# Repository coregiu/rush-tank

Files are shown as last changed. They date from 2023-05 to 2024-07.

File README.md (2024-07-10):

# Rush Tank
Rush Tank(简称Ruke)是利用51单片机、L298N电机驱动、PS2手柄、坦克坦克底盘、1000RPM的带霍尔效应编码器的JGB37 520调速电机DIY实现的PS2摇控坦克，提供精确速度控制，加减速，遥控体验绝佳。

## 功能说明
#### 遥控坦克正常行驶
可通过PS2左侧摇杆控制坦克前进、后退、左转、右转。

#### 加减速控制
可通过PS2右侧摇杆控制坦克加速、减速、向左前行进、向右前行进。

## 设计说明

#### 硬件设计

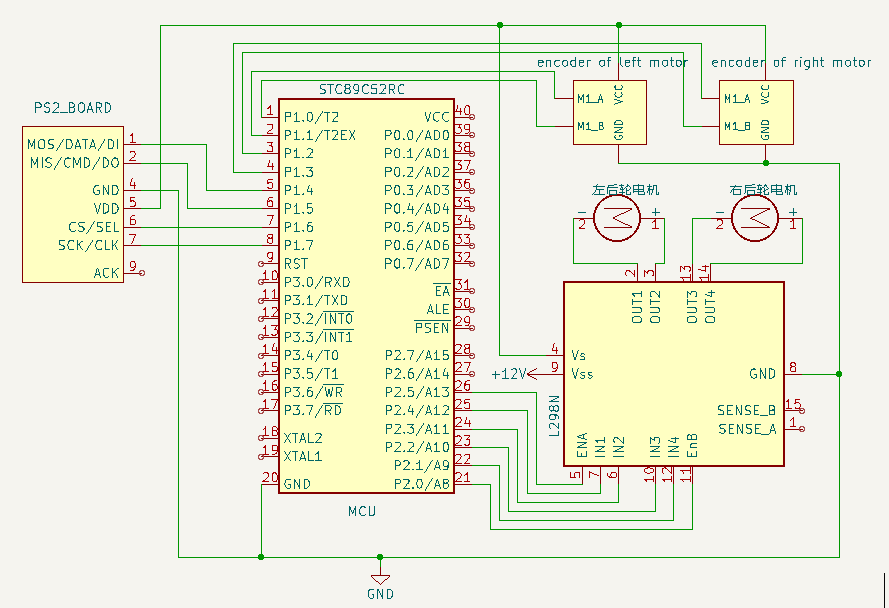
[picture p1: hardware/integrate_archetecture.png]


详细参照：[硬件设计说明](hardware/README.md)

#### 软件设计
##### 实现原理及状态图
如硬件设计所示，RUKE采用两组电机控制，使用L298N电机驱动控制实现RUKE行驶控制。采用PS2手柄作为控制输入。
因此，RUKE实现原理就是将PS2命令接收转换成控制L298N的信号即完成RUKE行驶控制。

L298N分两路电机控制，每路电机有三个信号引脚： 输入1（后文叫FRONT），输入2（后文叫BACK），使能（后文叫ENABLE）。
控制状态如下：
- 输入1=1， 输入2=0， 前进方向。 使能引脚默认接高电平，也可通过PWM控制速度。
- 输入1=0， 输入2=1， 后退方向。
- 输入1=0， 输入2=0， 停止。

因此RUKE实现逻辑是：
- 前进：两个电机都前进方向，使能全部高电平。
- 后退：两个电机都后退方向，使能全部高电平。
- 左转：左侧电机停止，右侧电机前进。
- 右转：右侧电机停止，左侧电机前进。
- 左向调头：左侧电机后退，右侧电机前进。
- 右向调头：右侧电机后退，左侧电机前进。
- 调速、左右向微调都是通过对ENABLE信号脚进行PWM控制实现速度微调。

因此，RUKE状态设计如下图，分小车行驶方向状态、速度状态两种状态，分别由PS2左、右两侧摇杆控制：
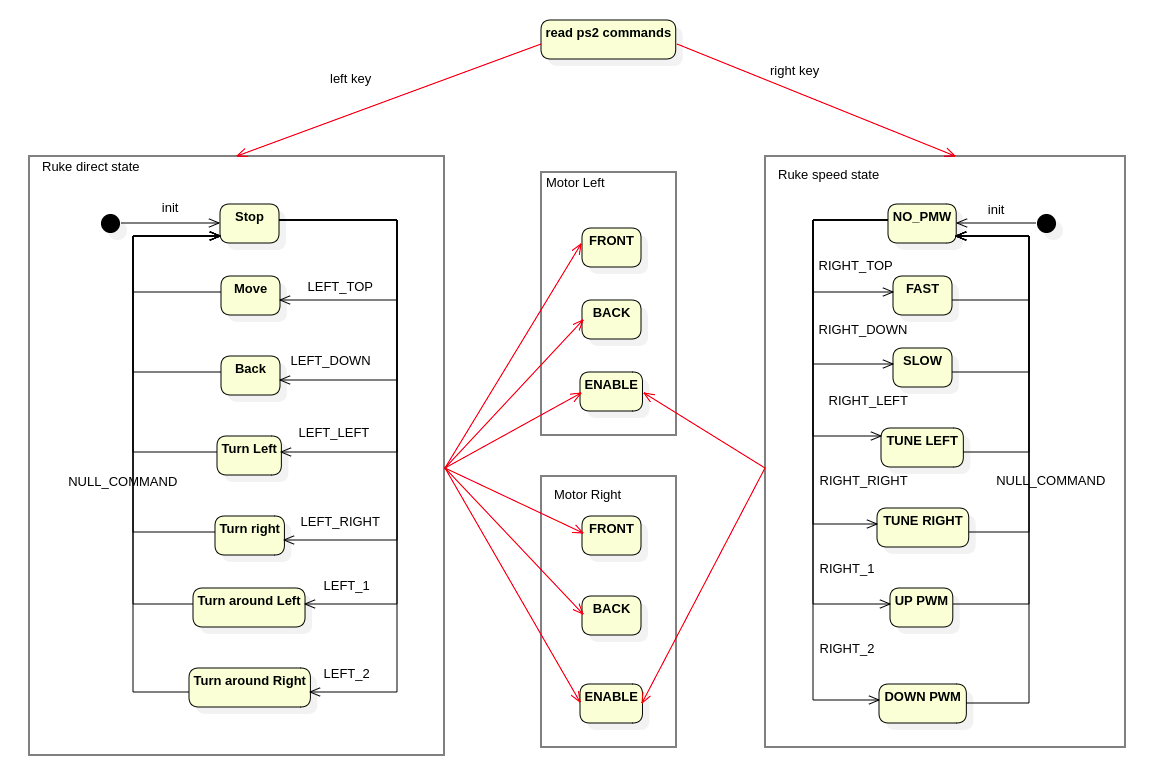
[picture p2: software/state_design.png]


##### 详细类图设计
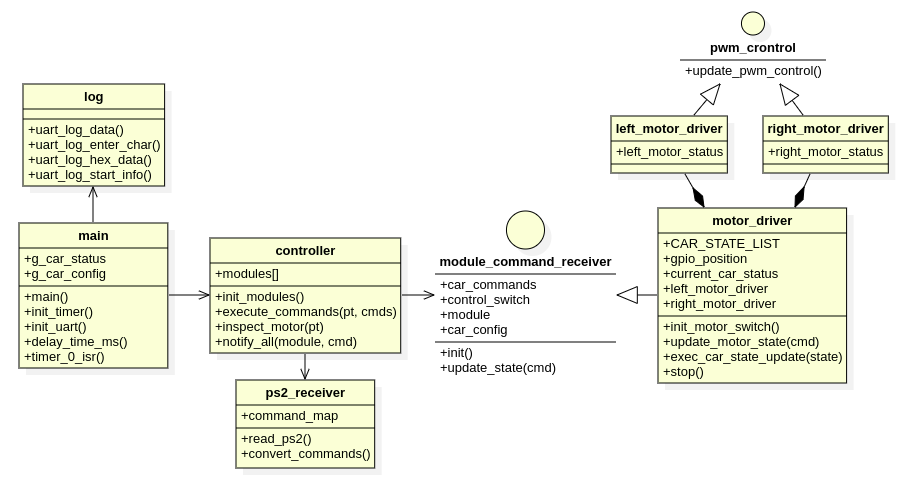
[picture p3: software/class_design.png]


详细参照：[软件设计说明和代码](software/README.md)

## PS2按键功能

| 按键 | 功能 | 监控指示灯 |
| --- | --- | --- |
| 左侧上键 | 坦克前进，长按有效，放开停止 | P0_0 |
| 左侧下键 | 坦克后退，长按有效，放开停止 | P0_1 |
| 左侧左键 | 坦克左转，长按有效，放开停止 | P0_2 |
| 左侧右键 | 坦克右转，长按有效，放开停止 | P0_3 |
| 左侧1键  | 顺时针快速调头 | P0_4 |
| 左侧2键  | 逆时针快速调头 | P0_5 |
| 右侧上健 | 加速行驶 | P0_0 |
| 右侧下键 | 减速行驶 | P0_1 |
| 右侧左键 | 坦克向左微调80%PWM，长按有效，放开恢复正常行驶  | P0_2 |
| 右侧右键 | 坦克向右微调80%PWM，长按有效，放开恢复正常行驶  | P0_3 |
| 右侧1键  | 同时按住左侧健时，直接最大速度行驶。 不按左侧健时，微调行驶角度，PWN加20% | P0_4 |
| 右侧2键  | 同时按住左侧健时，直接最小速度行驶。 不按左侧健时，微调行驶角度，PWN减20% | P0_5 |

## 成品效果

##### 视频

https://www.bilibili.com/video/BV1Zu411p7aM/?spm_id_from=333.999.0.0

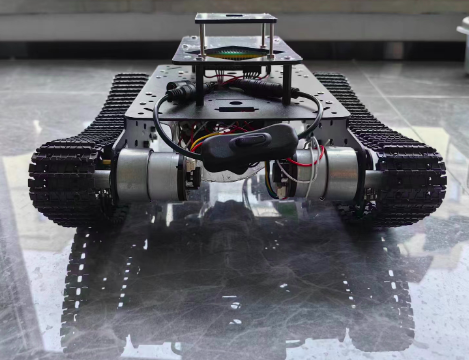
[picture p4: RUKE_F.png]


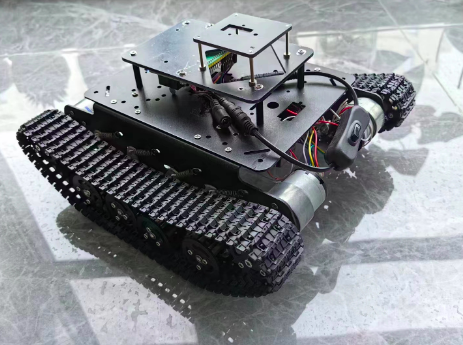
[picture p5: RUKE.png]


## 硬件模块及工具清单：

| 模块 | 说明 | 价格(元) |
| --- | --- | --- |
| 51单片机 | 单片机 STC89C52RC芯片，11.0592晶振。 | 40 |
| 坦克底盘 | 坦克底盘及M3铜柱螺丝若干，底盘带4个直流电机。 | 350 |
| ps2手柄 | 无线的那种，会带接收器。 | 40 |
| L298N电机驱动 | 12V供电，同时带5V输出电压。 | 4 |
| JGB37 520减速电机  | JGB37 520减速电机 * 2 | 每个35元 |
| 电池及充电器  | 12V锂电池和12V充电器 | 35 |
| 各种接线 | 各种公对公，母对母杜邦线若干，DIY铜线，漆包线，转接头，接线器等 | 10 |

另外音乐芯片组装需要电烙铁焊接，组装时可能需要万用表做些测试。如果对焊接不熟悉，还是买现成的模块比较合适。以上东西都可以在网上买到。

## 使用的相关工具软件：

#### OS： Ubuntu 20.04

#### 硬件设计工具KiCAD

安装：https://docs.kicad.org/5.1/zh/getting_started_in_kicad/getting_started_in_kicad.html

#### 软件设计开发工具:

- 软件设计工具： StarUML  https://staruml.io/download

- 开发IDE： VSCODE

- 编译软件： sdcc/packihx, cmake

ubuntu下安装： sudo apt-get install sdcc

- 烧录软件：stcflash

ubuntu下安装： 从社区下载到本地，社区地址：https://github.com/laborer/stcflash

将stcflash.py文件解压到/usr/local/bin。 并去掉后缀名。

- 依赖： python3, python-pip3, python serial

安装python serial: https://www.geeksforgeeks.org/how-to-install-python-serial-package-on-linux/

如果执行: stcflash报错： usr/bin/env: ‘python’: No such file or directory

执行以下命令解决： sudo ln -s /usr/bin/python3 /usr/bin/python

- 串口调试工具： comtool

安装： sudo pipe3 install comtool

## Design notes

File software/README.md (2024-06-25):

## 整体设计



## 代码结构说明
整体代码分五个模块，一个接口结构体和一个main函数。

controller：代表MCU，作中心控制，接收PS2数据，并把数据转换成命令通知给各驱动模块干活。

ps2_receiver： PS2接收模块，接收PS2传过来的数据，并转换成内部命令。

module_command_receiver： 命令接收执行工作模块接口，定义内部命令，抽象模块初始化和命令执行接口。

led_group： LED灯组模块，接收主控中灯光开关指令，根据PS2传递的指令切换灯组开关。

music_switch： 音乐驱动模块，接收主控中音乐相关指令，可控制音乐播放。

motor_driver： 电机驱动模块，接收主控中电机相关指令，控制底盘前进、后退、左转和右转。

servos_driver：舵机控制模块，接收主控中舵机相关指令，控制舵机前后、左右移动以及复位。

pca9685： 舵机驱动使能模块，通过IIC连接pca9685驱动，将servos_driver中的指令下到具体舵机上。

## 编译烧录：

第一步，编译：

```shell
$cd {work_path}/ruke/software/code
$mkdir build
$cd build
$cmake ..
$make
$ls src
```模块，接收主控中舵机相关指令，控制舵机前后、左右移动以及复位。

pca9685： 舵机使能

## 编译烧录：

第一步，编译：

```shell
$cd {work_path}/ruke/software/code
$mkdir build
$cd build
$cmake ..
$make
$ls src
```

如果个人娱乐不想写cmake文件，就下面这样

```shell
$sudo sdcc led_basic.c -o led_basic.ihx
```

第二步，转换成可烧录的hex文件：

```shell
$cd src
$packihx RUKE.ihx > RUKE.hex
```

第三步，烧录文件到MCU：

```shell
$sudo stcflash RUKE.hex
```

此命令会自动寻找USB口发命令。如果有多个USB口，需要指定相应端口。

```shell
$sudo stcflash RUKE.hex --port /dev/ttyUSB0
```

## PS2通讯说明：

购买PS2后老板都会发教程和代码的。

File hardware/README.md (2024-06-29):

## 整体设计



## 模块说明

#### 坦克底盘
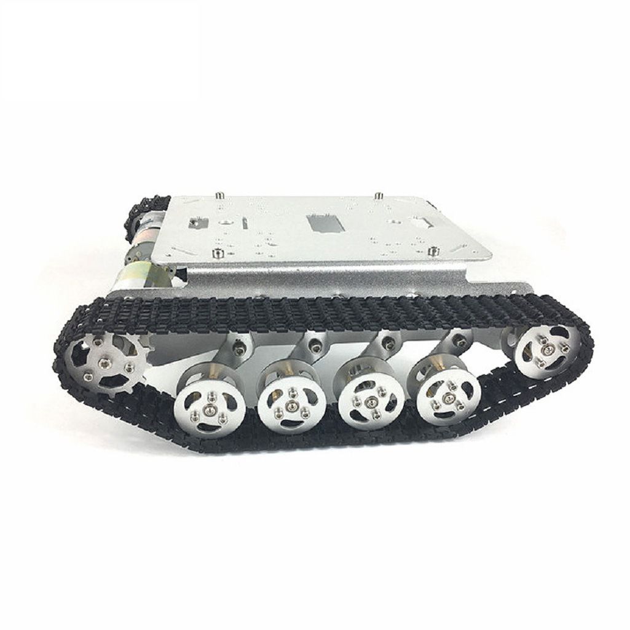
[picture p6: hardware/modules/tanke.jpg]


外购坦克底盘。

#### JGB37 520带霍尔编码器减速电机
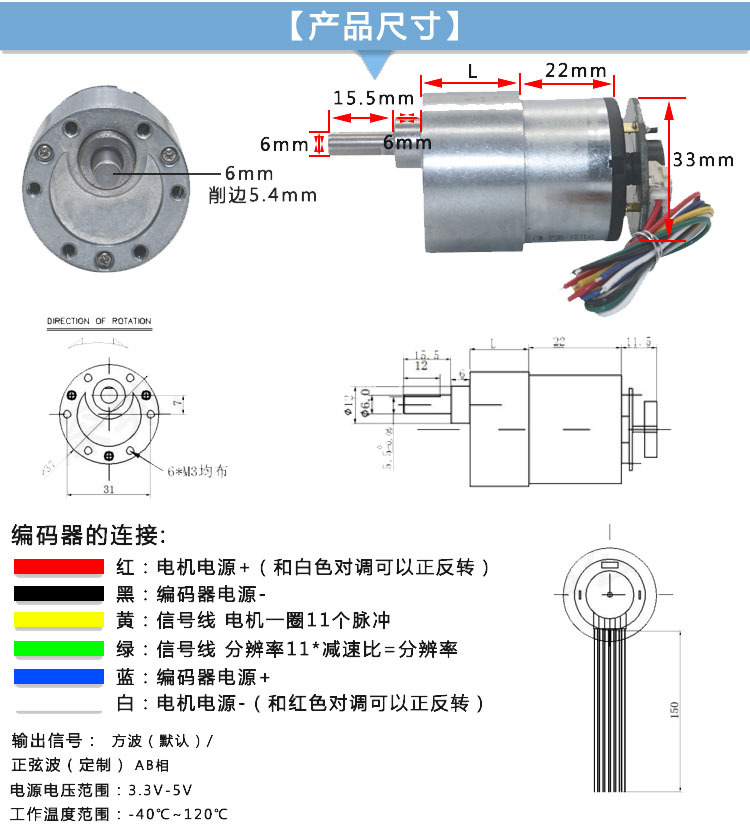
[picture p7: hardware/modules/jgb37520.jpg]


外购坦克底盘。

#### 控制模块
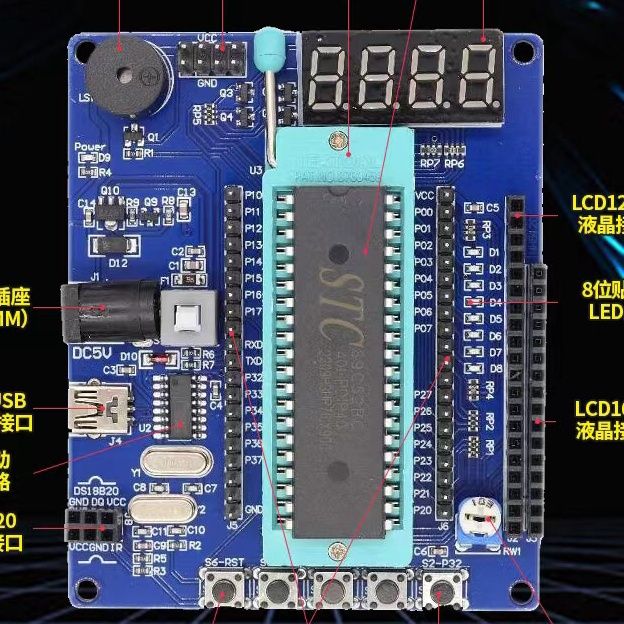
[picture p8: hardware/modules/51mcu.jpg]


使用51单片机（STC89C52RC）作为控制中心，其中P0口系列自带LED灯，为指令监控显示灯； P2.0-P2.5 为电机控制口，P2.6 为音乐开关。P2.7为灯组开关，P1.4-P1.7为PS2通信口。
晶振频率：11.0592

| GPIO | 连接口 | 初始值  | 说明 |
| ---- | --- | --- | --- |
| P2_0 | L298N_EnB 右轮使能 | 0 | |
| P2_1 | L298N_IN4 右轮前进高电平 | 0 | |
| P2_2 | L298N_IN3 右轮后退高电平 | 0 | |
| P2_3 | L298N_IN2 左轮前进高电平 | 0 | |
| P2_4 | L298N_IN1 左轮后退高电平 | 0 | |
| P2_5 | L298N_EnA 左轮使能 | 0 | |
| P1_0 | 左电机B信号 | 0 | |
| P1_1 | 左电机A信号 | 0 | |
| P1_2 | 左电机B信号 | 0 | |
| P1_3 | 左电机A信号 | 0 | |
| P1_4 | PS2_D1/DATA | default | |
| P1_5 | PS2_D0/CMD | default | |
| P1_6 | PS2_CS | default | |
| P1_7 | PS2_CLK | default | |
| P0_0 | 自带LED1 | 1 | 1命令时点亮 |
| P0_1 | 自带LED2 | 1 | 2命令时点亮 |
| P0_2 | 自带LED3 | 1 | 3命令时点亮 |
| P0_3 | 自带LED4 | 1 | 4命令时点亮 |
| P0_4 | 自带LED5 | 1 | 5命令时点亮 |
| P0_5 | 自带LED6 | 1 | 6命令时点亮 |
| P0_6 | 自带LED7 | 1 | 7命令时点亮 |
| P0_7 | 自带LED8 | 1 | 8命令时点亮 |

#### 电机驱动模块
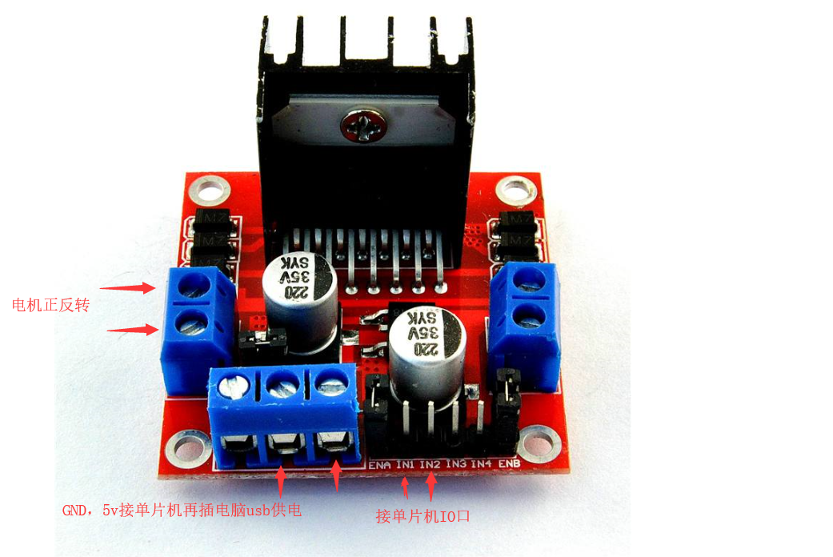
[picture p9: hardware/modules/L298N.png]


使用L298N电机驱动，左右轮分两组控制。

12V输入电压，5V输出电压为控制单板、音乐板、LED灯、PS2通信模块供电。

#### 遥控通信模块

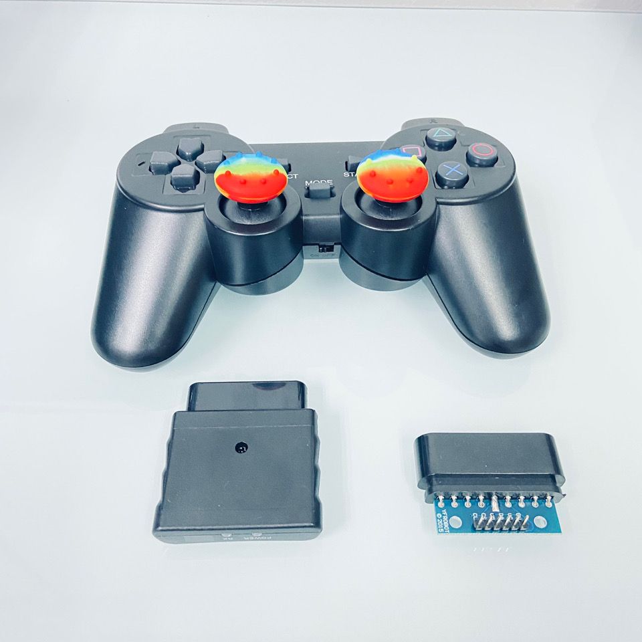
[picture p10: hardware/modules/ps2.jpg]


使用PS2通信模块进行遥控。控制键说明：

| 按键 | 功能 | 监控指示灯 |
| --- | --- | --- |
| 左侧上键 | 坦克前进，长按有效，放开停止 | P0_0 |
| 左侧下键 | 坦克后退，长按有效，放开停止 | P0_1 |
| 左侧左键 | 坦克左转，长按有效，放开停止 | P0_2 |
| 左侧右键 | 坦克右转，长按有效，放开停止 | P0_3 |
| 左侧1键  | 顺时针快速调头 | P0_4 |
| 左侧2键  | 逆时针快速调头 | P0_5 |
| 右侧上健 | 加速行驶 | P0_0 |
| 右侧下键 | 减速行驶 | P0_1 |
| 右侧左键 | 坦克向左微调80%PWM，长按有效，放开恢复正常行驶  | P0_2 |
| 右侧右键 | 坦克向右微调80%PWM，长按有效，放开恢复正常行驶  | P0_3 |
| 右侧1键  | 同时按住左侧健时，直接最大速度行驶。 不按左侧健时，微调行驶角度，PWN加20% | P0_4 |
| 右侧2键  | 同时按住左侧健时，直接最小速度行驶。 不按左侧健时，微调行驶角度，PWN减20% | P0_5 |

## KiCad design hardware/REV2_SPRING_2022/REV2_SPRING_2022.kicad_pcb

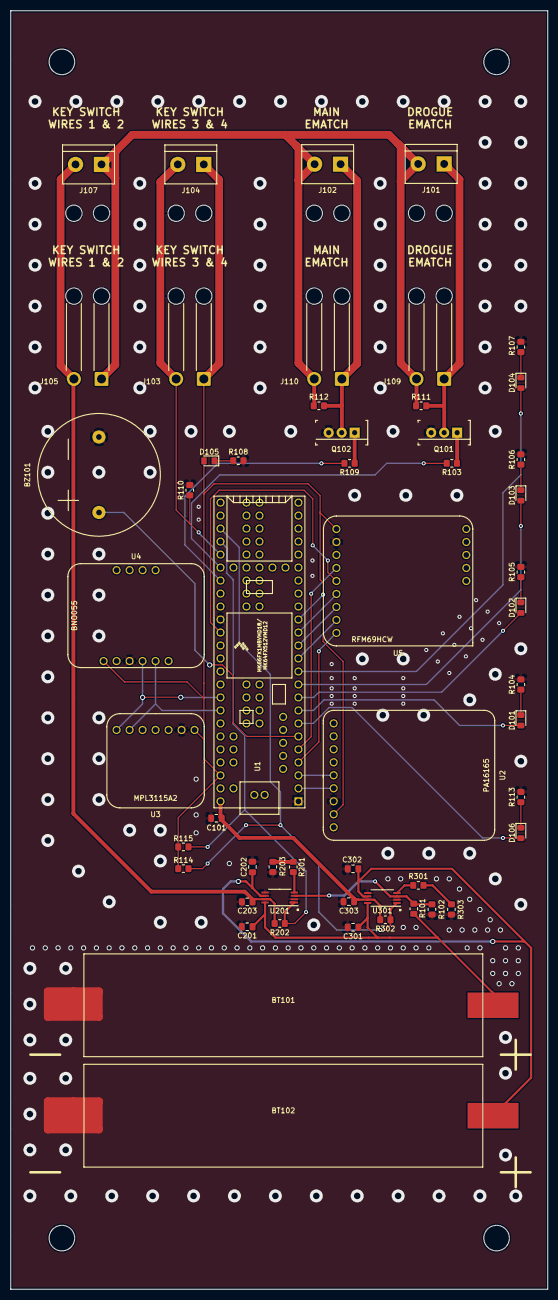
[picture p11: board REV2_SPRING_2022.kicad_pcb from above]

Board: 2 copper layers, 105.0 x 250.0 mm, 54 parts (0 on the bottom side), 43 nets.

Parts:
BT101, BT102: Battery_Cell; MyBatteryHolder_MPD_BH-18650-PC2
BZ101: Buzzer; Large_Buzzer_24mmOD_14.8mmPinDistance_1.0mmPinDiameter
C101, C201, C202, C203, C301, C302, C303: C_0.1u; C_0805_2012Metric_Pad1.18x1.45mm_HandSolder
D101, D102, D103, D104, D105, D106: LED; LED_0805_2012Metric_Pad1.15x1.40mm_HandSolder
J101, J102, J104, J107: Screw_Terminal_01x02; TerminalBlock_bornier-2_P5.08mm
J103, J105, J109, J110: Conn_01x02_Female; SolderWire-1sqmm_1x02_P5.4mm_D1.4mm_OD2.7mm_Relief2x
Q101, Q102: Q_NMOS_GDS; TO-220-3
R101: R_15k; R_0805_2012Metric_Pad1.20x1.40mm_HandSolder
R102: R_4.7k; R_0805_2012Metric_Pad1.20x1.40mm_HandSolder
R103, R109, R110, R111, R112, R114, R115, R202, R302: R_10k; R_0805_2012Metric_Pad1.20x1.40mm_HandSolder
R104, R105, R106, R107, R108, R113: R_750; R_0805_2012Metric_Pad1.20x1.40mm_HandSolder
R201, R203, R301, R303: R_200; R_0805_2012Metric_Pad1.20x1.40mm_HandSolder
U1: Teensy3.6_All_Pins; Teensy35_36_All_Pins
U2: PA16165_Breakout
U3: MPL3115A2_Breakout
U4: BNO055_Breakout
U5: RFM69HCW_Breakout
U201, U301: TPS2113ADRBR; TSSOP-8_4.4x3mm_P0.65mm

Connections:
/3.3V: D105.2, J103.1, J104.1, R114.1, R115.1, U1.15, U1.51, U2.8, U3.1, U4.1, U5.1
/BAT1: BT101.1, C201.1, C301.1, R101.1, U201.8, U301.8
/BAT2: BT102.1, C202.1, C302.1, U201.6, U301.6
/BUZZER: BZ101.1, U1.6
/CS0: U1.12, U5.8
/E-MATCH_TRIGGER_1: R103.2, U1.35
/E-MATCH_TRIGGER_2: R109.2, U1.36
/EMATCH_1+: J101.1, J109.1, Q101.2, R111.2
/EMATCH_2+: J102.1, J110.1, Q102.2, R112.2
/KEY_SWITCH_DIGITAL: J103.2, J104.2, R110.1, U1.34
/LED_0: D106.2, U1.7
/LED_1: D101.2, U1.8
/LED_2: D102.2, U1.9
/LED_3: D103.2, U1.10
/LED_4: D104.2, U1.11
/MISO0: U1.14, U5.6
/MOSI0: U1.13, U5.7
/PWM: U1.4, U5.9
/RX1: U1.2, U2.6
/SCK: U1.40, U5.5
/SCL0: U1.46, U3.6, U4.5
/SCL2: U1.5, U5.4
/SDA0: U1.45, U3.7, U4.4
/TPS2113A for E-match/VSNS: R101.2, R102.1, U201.3, U301.3
/TPS_1_STAT: R114.2, R302.2, U1.32, U301.1
/TPS_2_STAT: R115.2, R202.2, U1.33, U201.1
/TX1: U1.3, U2.5
/V_EMATCH: J101.2, J102.2, J105.1, J107.1, J109.2, J110.2, R111.1, R112.1
/V_EMATCH_TO_KEY_SWITCH: C203.1, J105.2, J107.2, R202.1, U201.7
/V_TEENSY: C101.1, C303.1, R302.1, U1.53, U301.7
GND: BT101.2, BT102.2, BZ101.2, C101.2, C201.2, C202.2, C203.2, C301.2, C302.2, C303.2, Q101.3, Q102.3, R102.2, R104.2, R105.2, R106.2, R107.2, R108.2, R110.2, R113.2, R203.1, R303.1, U1.1, U1.39, U2.7, U3.2, U4.3, U5.2, U201.2, U201.5, U301.2, U301.5
unnamed: D101.1, R104.1
unnamed: D102.1, R105.1
unnamed: D103.1, R106.1
unnamed: D104.1, R107.1
unnamed: D105.1, R108.1
unnamed: D106.1, R113.1
unnamed: Q101.1, R103.1
unnamed: Q102.1, R109.1
unnamed: R201.1, R203.2
unnamed: R201.2, U201.4
unnamed: R301.1, R303.2
unnamed: R301.2, U301.4

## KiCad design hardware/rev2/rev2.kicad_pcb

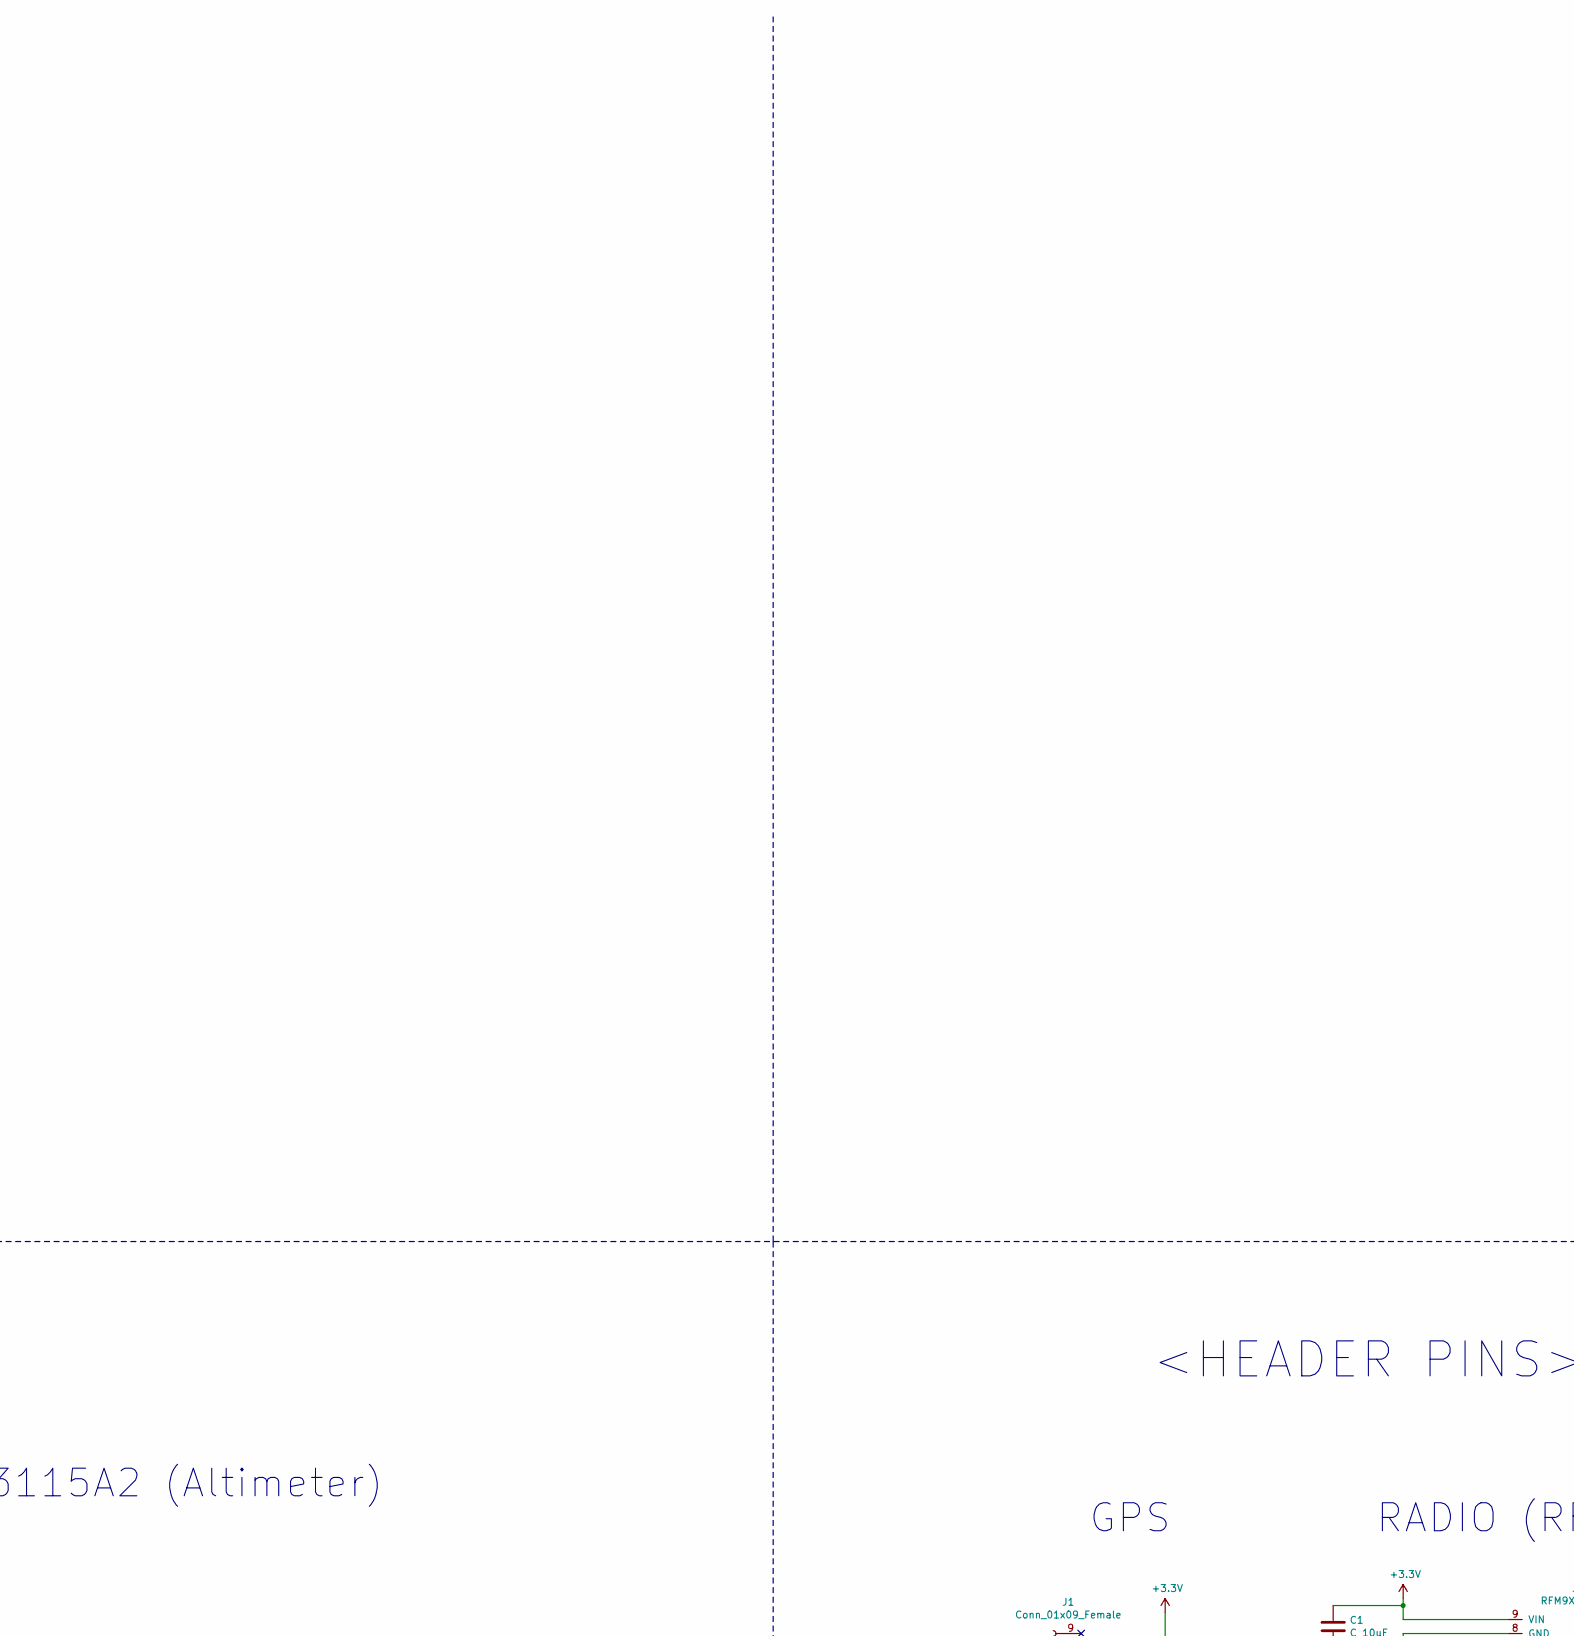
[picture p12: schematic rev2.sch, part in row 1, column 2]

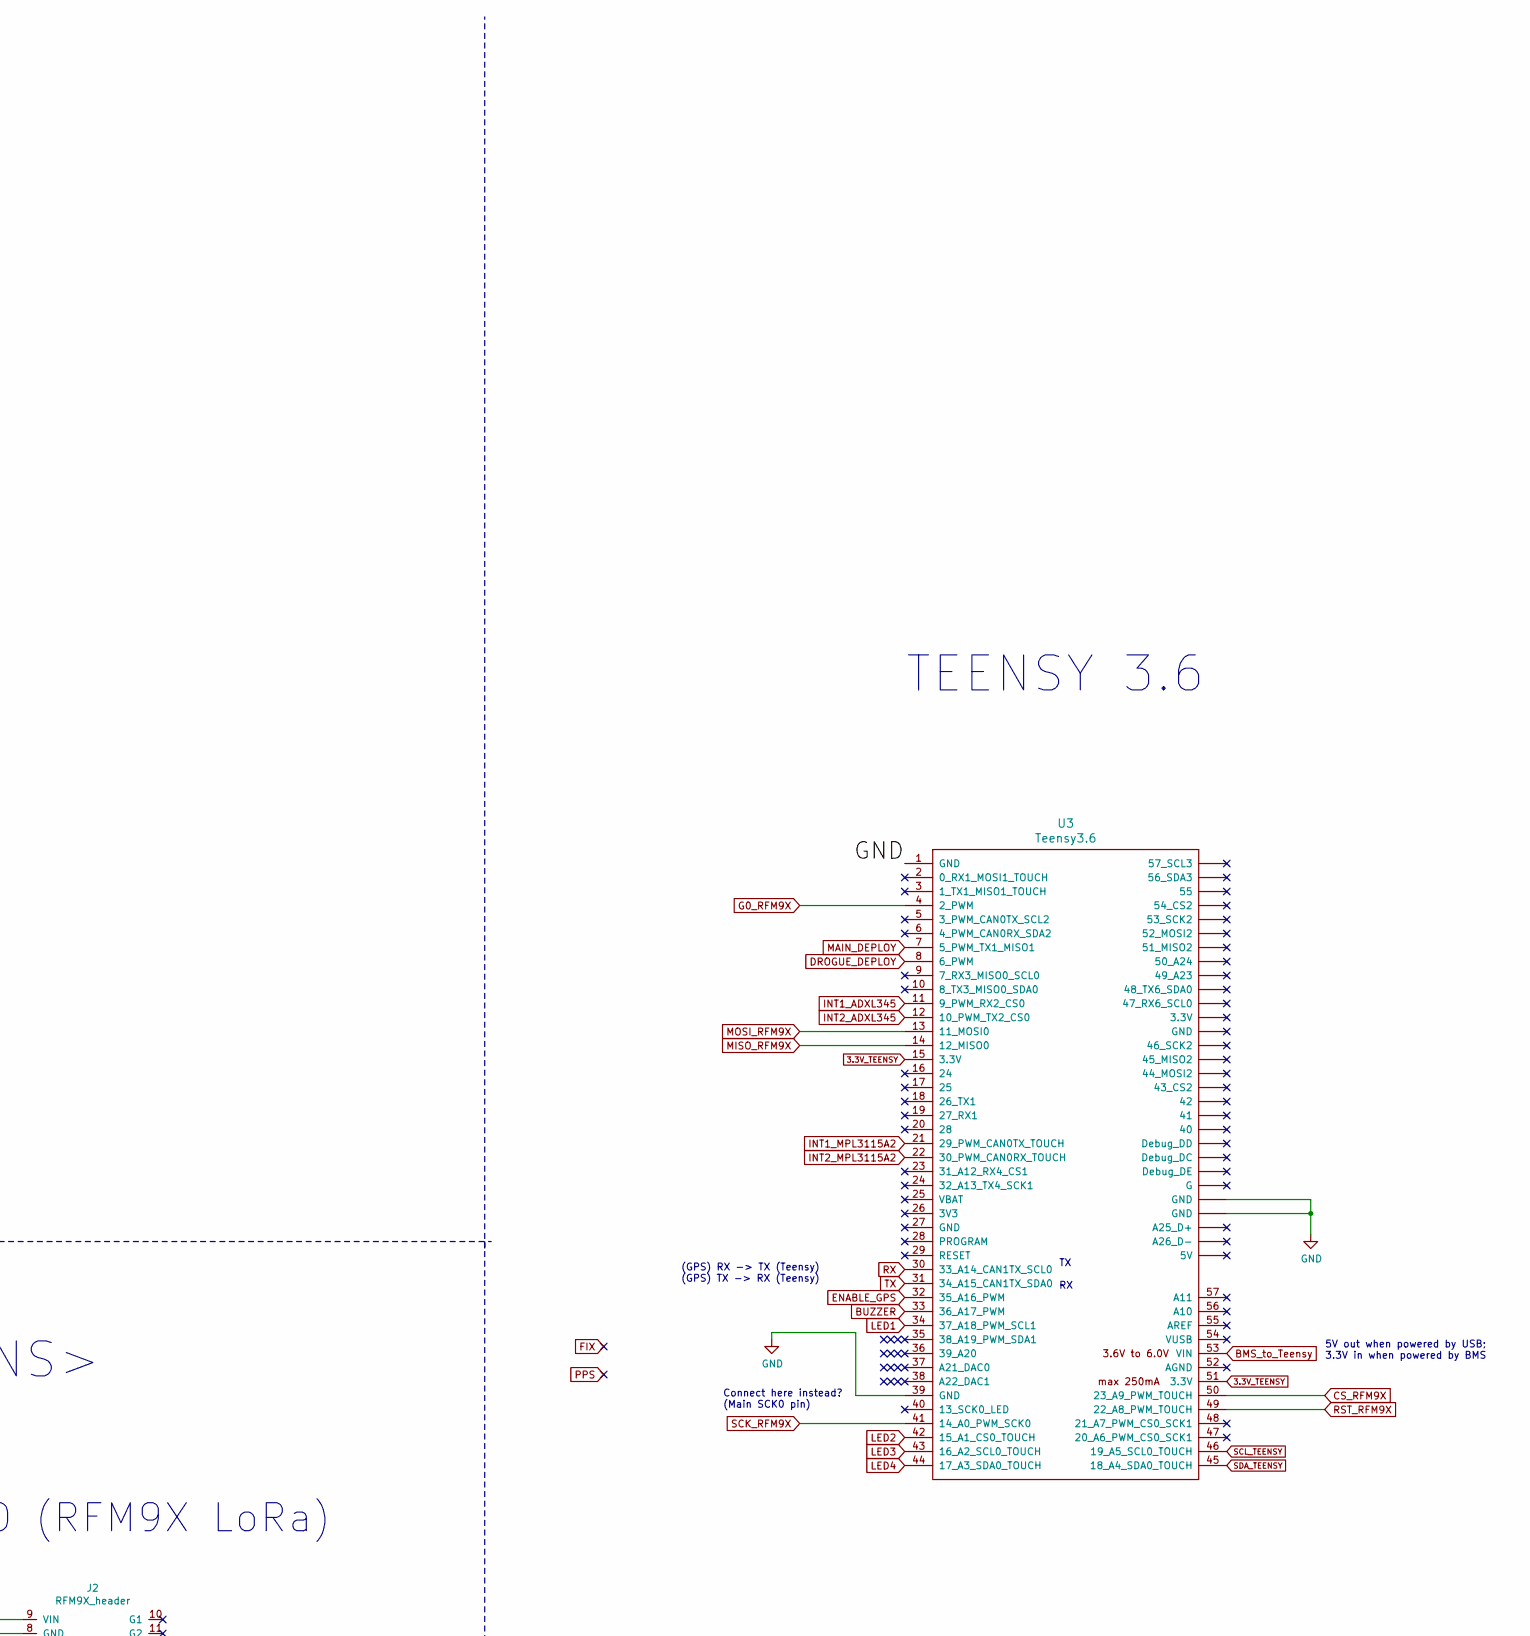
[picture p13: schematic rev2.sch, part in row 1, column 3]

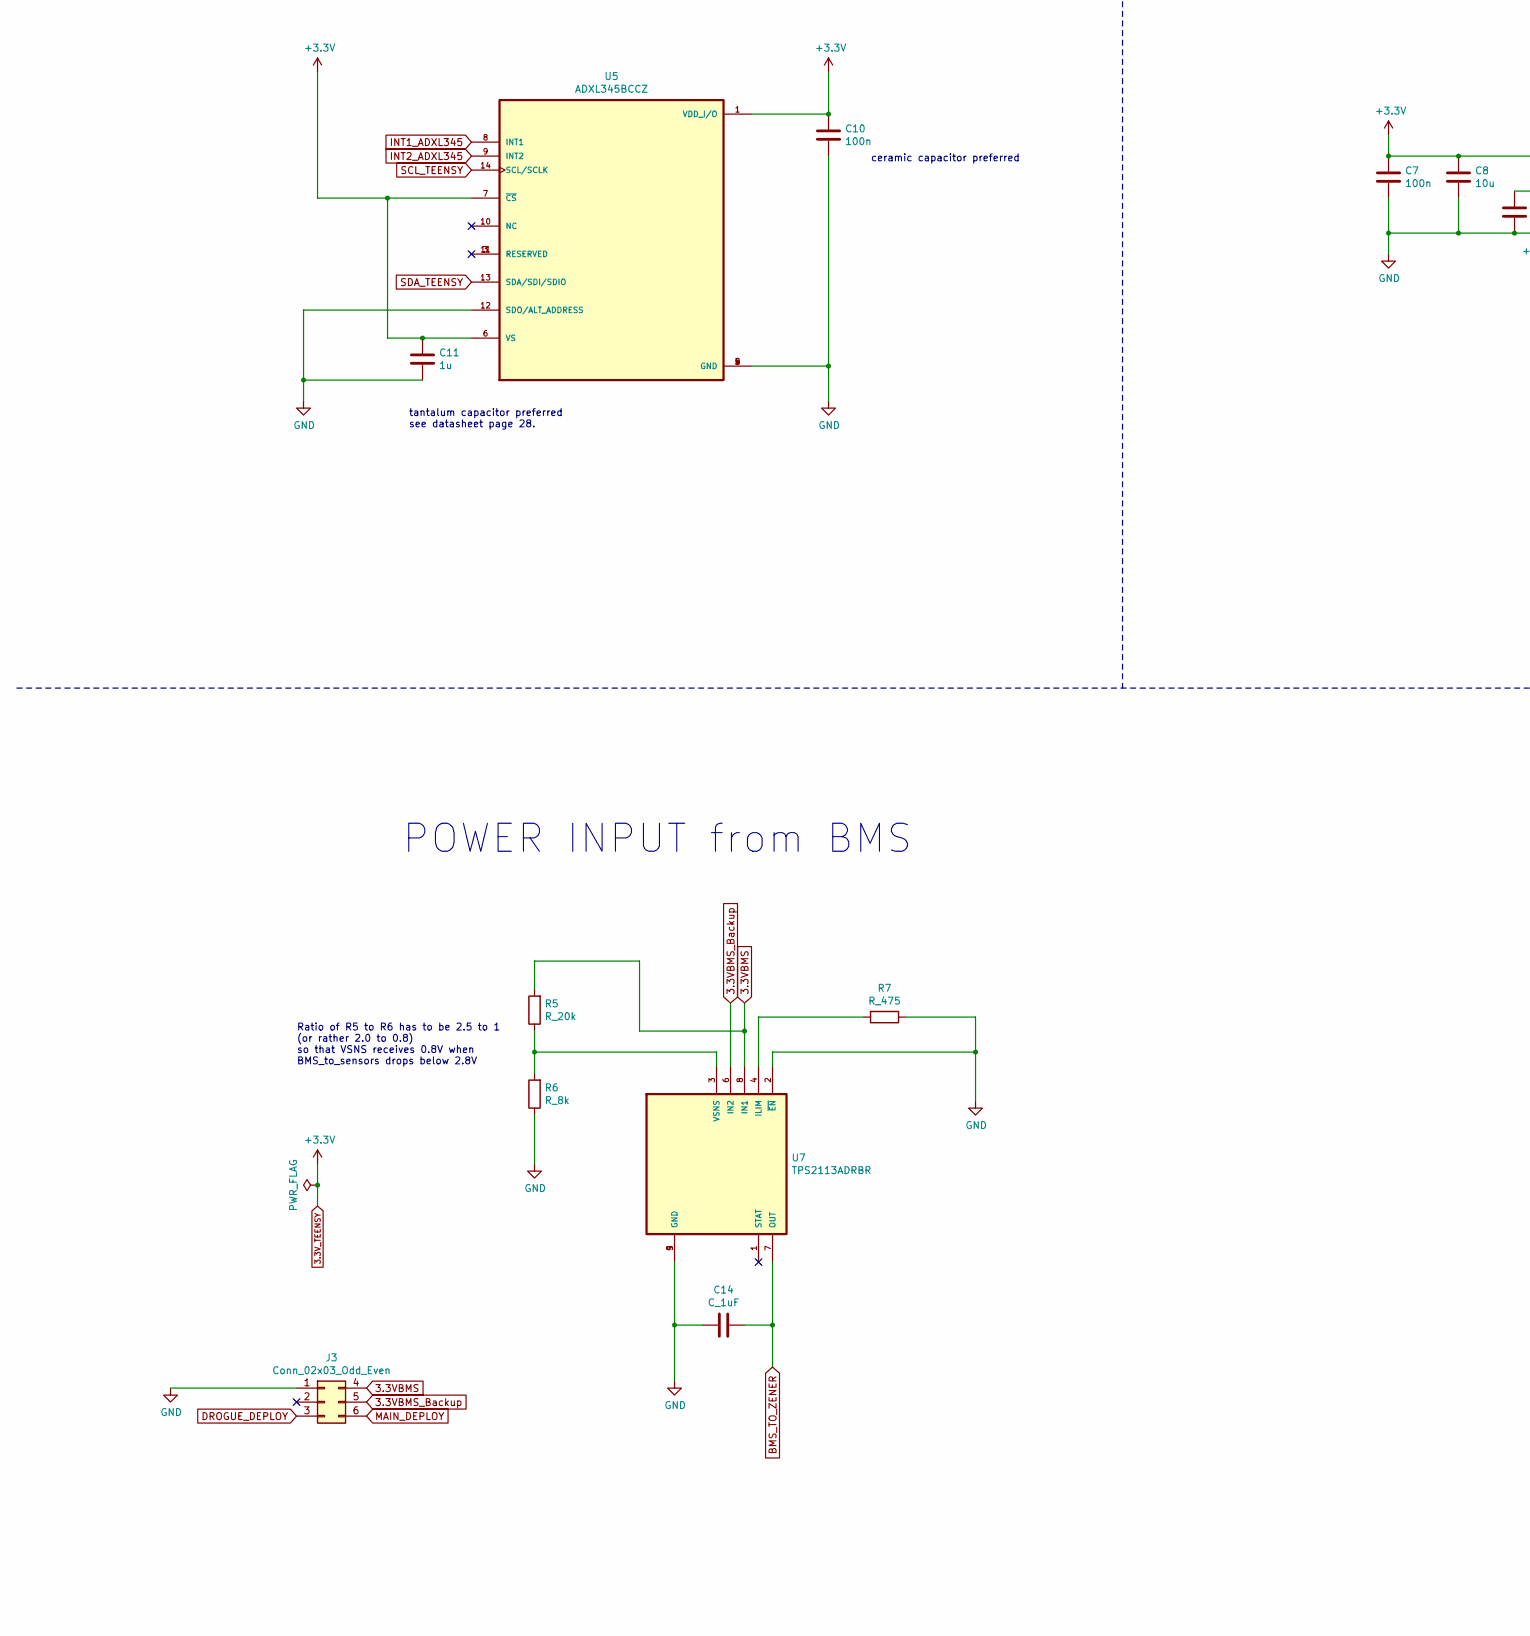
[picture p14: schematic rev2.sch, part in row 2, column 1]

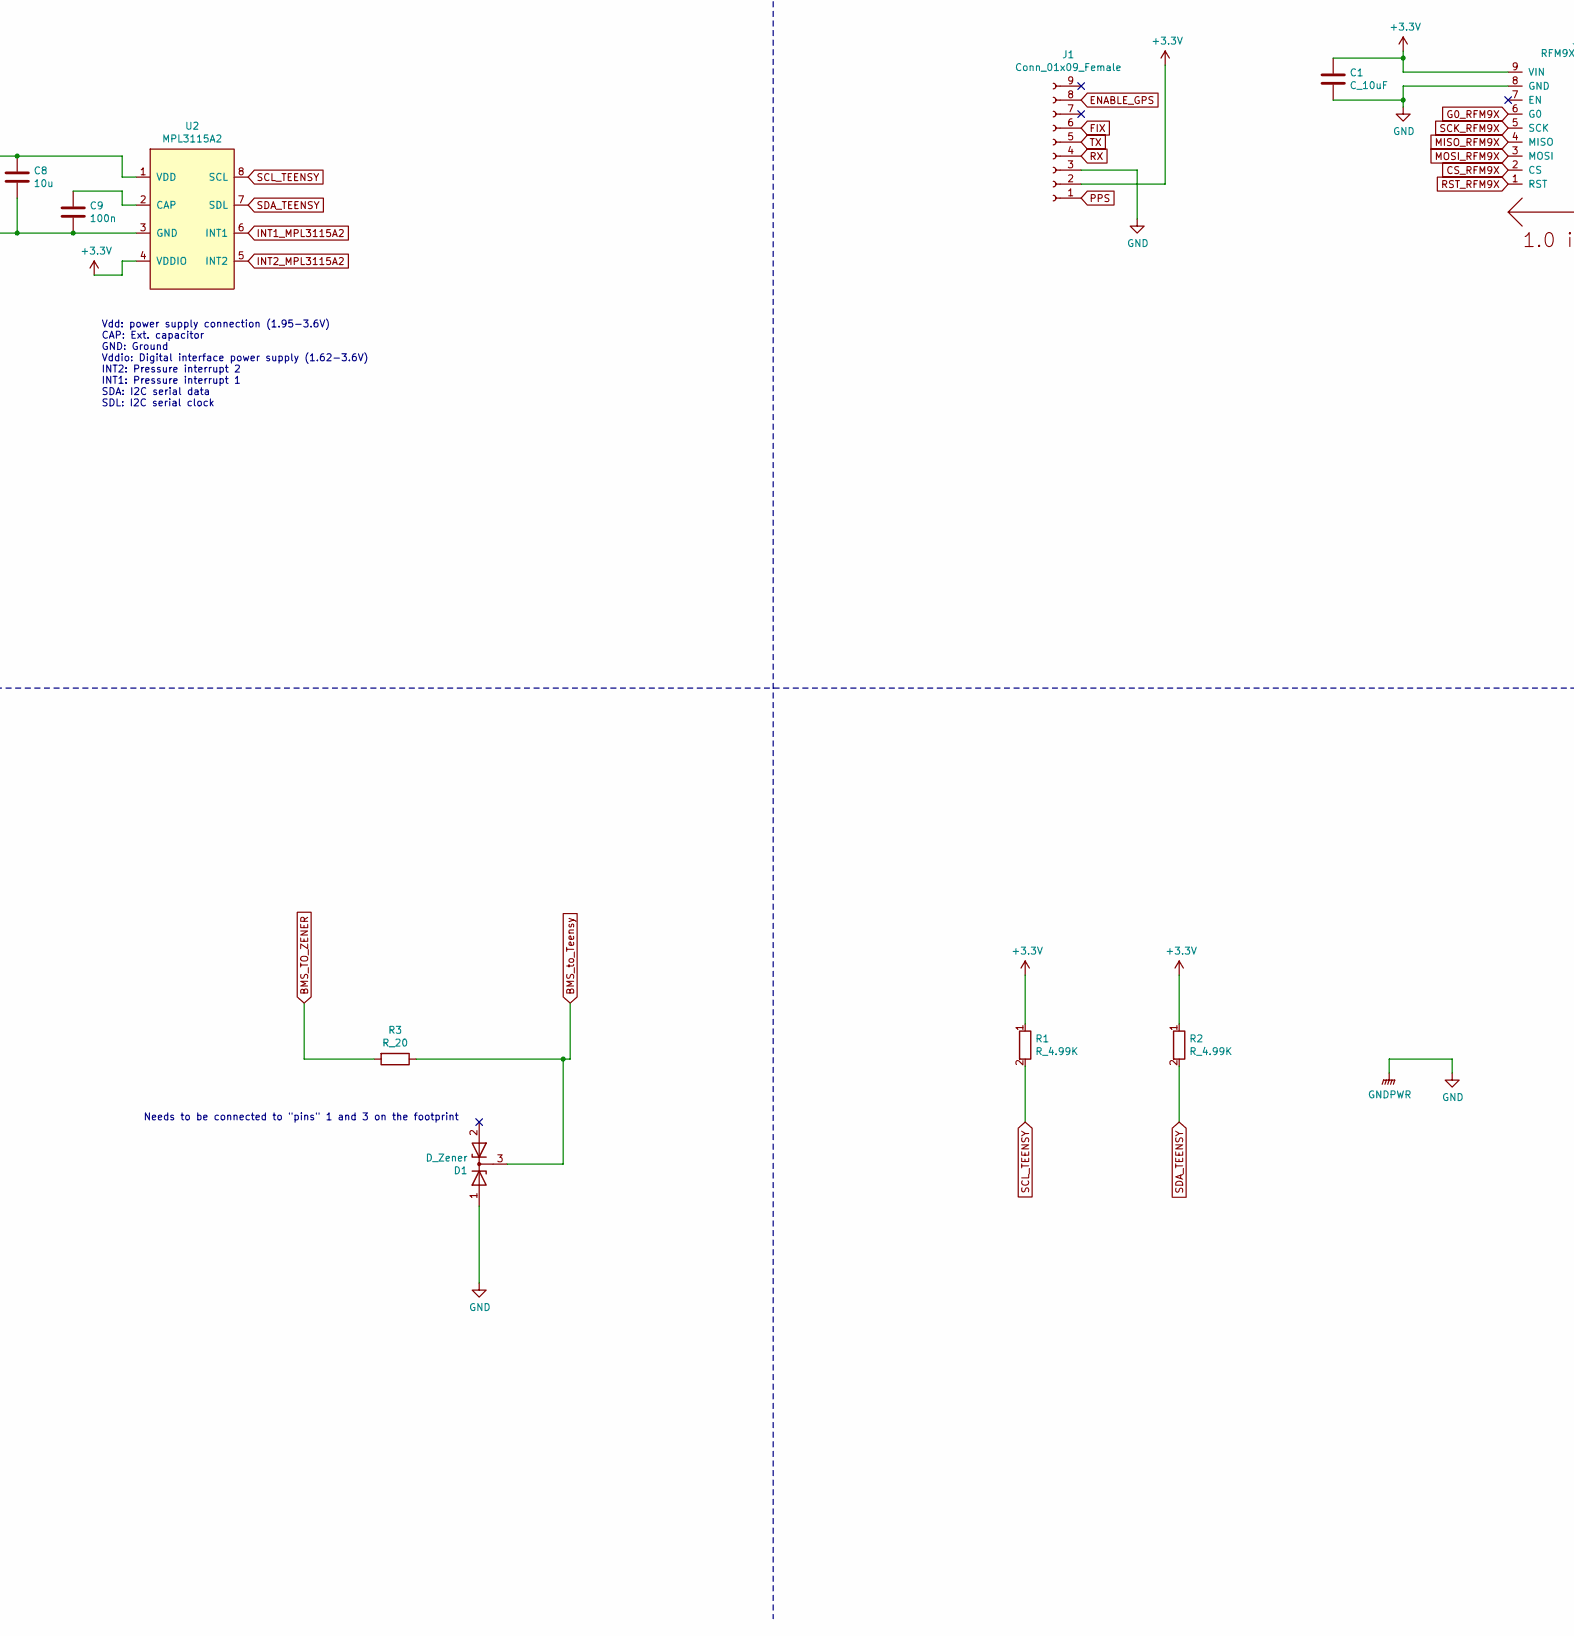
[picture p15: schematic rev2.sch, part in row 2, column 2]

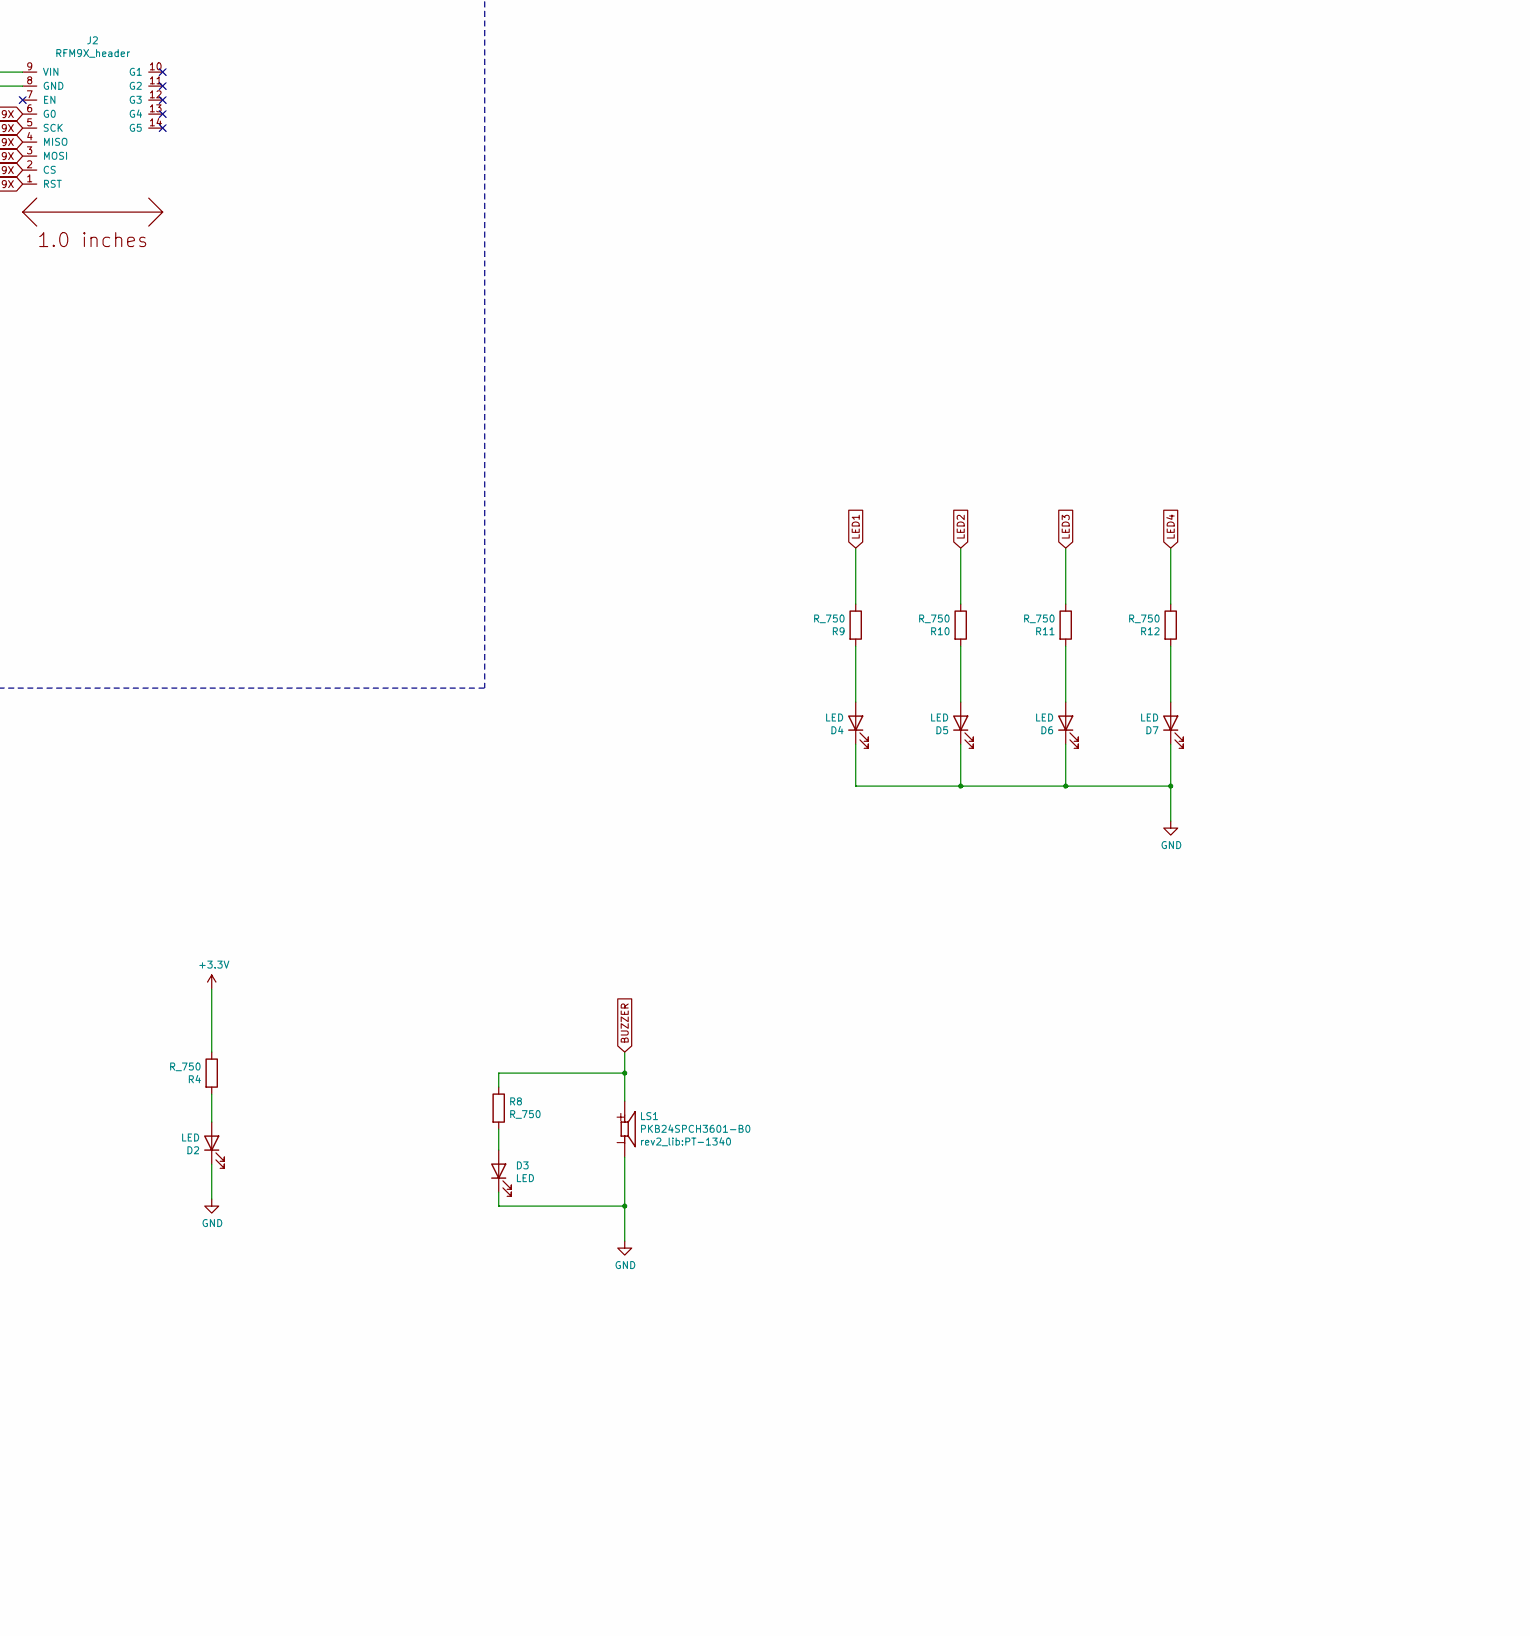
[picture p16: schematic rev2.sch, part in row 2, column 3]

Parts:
C1: C_10uF; C_0805_OEM; MPN 1276-1052-1-ND
C7, C9: 100n; C_0805_OEM
C8: 10u; C_0805_OEM
C10: 100n; C_0805_OEM; MPN 478-3352-1-ND
C11: 1u; C_0805_OEM; MPN 1276-2887-1-ND
C14: C_1uF; C_0805_OEM; MPN 1276-2887-1-ND
D1: D_Zener; SOT-23
D2, D3, D4, D5, D6, D7: LED; AA3528LSECKT-J4
J1: Conn_01x09_Female; PinSocket_1x09_P2.54mm_Vertical
J2: RFM9X_header
J3: Conn_02x03_Odd_Even; Molex_Nano-Fit_105312-1106
LS1: PKB24SPCH3601-B0; PT-1340; PARTREV March 24, 2017
R1, R2: R_4.99K; R_0805_OEM
R3: R_20; R_0805_OEM
R4, R8, R9, R10, R11, R12: R_750; R_0805_OEM
R5: R_20k; R_0805_OEM; MPN 311-475CRCT-ND
R6: R_8k; R_0805_OEM; MPN 311-475CRCT-ND
R7: R_475; R_0805_OEM; MPN 311-475CRCT-ND
U2: MPL3115A2
U3: Teensy3.6; Teensy3-6
U5: ADXL345BCCZ; ADXL345
U7: TPS2113ADRBR

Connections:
3.3VBMS: J3.4, R5.2, U7.8 (IN1)
3.3VBMS_Backup: J3.5, U7.6 (IN2)
3.3V_TEENSY: C1.1, C7.1, C8.1, C10.1, C11.1, J1.2, J2.9 (VIN), R1.1, R2.1, R4.1, U2.1 (VDD), U2.4 (VDDIO), U3.15 (3.3V), U3.51 (3.3V), U5.1 (VDD_I/O), U5.6 (VS), U5.7 (~CS)
BMS_TO_ZENER: C14.1, R3.2, U7.7 (OUT)
BMS_to_Teensy: D1.3 (K), R3.1, U3.53 (VIN)
BUZZER: LS1.P, R8.1, U3.33 (36_A17_PWM)
CS_RFM9X: J2.2 (CS), U3.50 (23_A9_PWM_TOUCH)
DROGUE_DEPLOY: J3.3, U3.8 (6_PWM)
ENABLE_GPS: J1.8, U3.32 (35_A16_PWM)
FIX: J1.6
G0_RFM9X: J2.6 (G0), U3.4 (2_PWM)
GND: C1.2, C7.2, C8.2, C9.2, C10.2, C11.2, C14.2, D1.1 (A), D2.1 (K), D3.1 (K), D4.1 (K), D5.1 (K), D6.1 (K), D7.1 (K), J1.3, J2.8 (GND), J3.1, LS1.N, R6.1, R7.1, U2.3 (GND), U3.1 (GND), U3.39 (GND), U3.~ (3.3V), U5.2 (GND), U5.4 (GND), U5.5 (GND), U5.12 (SDO/ALT_ADDRESS), U7.2 (~EN), U7.5 (GND), U7.9 (GND)
INT1_ADXL345: U3.11 (9_PWM_RX2_CS0), U5.8 (INT1)
INT1_MPL3115A2: U2.6 (INT1), U3.21 (29_PWM_CAN0TX_TOUCH)
INT2_ADXL345: U3.12 (10_PWM_TX2_CS0), U5.9 (INT2)
INT2_MPL3115A2: U2.5 (INT2), U3.22 (30_PWM_CAN0RX_TOUCH)
LED1: R9.1, U3.34 (37_A18_PWM_SCL1)
LED2: R10.1, U3.42 (15_A1_CS0_TOUCH)
LED3: R11.1, U3.43 (16_A2_SCL0_TOUCH)
LED4: R12.1, U3.44 (17_A3_SDA0_TOUCH)
MAIN_DEPLOY: J3.6, U3.7 (5_PWM_TX1_MISO1)
MISO_RFM9X: J2.4 (MISO), U3.14 (12_MISO0)
MOSI_RFM9X: J2.3 (MOSI), U3.13 (11_MOSI0)
unnamed: C9.1, U2.2 (CAP)
unnamed: D2.2 (A), R4.2
unnamed: D3.2 (A), R8.2
unnamed: D4.2 (A), R9.2
unnamed: D5.2 (A), R10.2
unnamed: D6.2 (A), R11.2
unnamed: D7.2 (A), R12.2
unnamed: R5.1, R6.2, U7.3 (VSNS)
unnamed: R7.2, U7.4 (ILIM)
unnamed: U5.3 (RESERVED), U5.11 (RESERVED)
PPS: J1.1
RST_RFM9X: J2.1 (RST), U3.49 (22_A8_PWM_TOUCH)
RX: J1.4, U3.30 (33_A14_CAN1TX_SCL0)
SCK_RFM9X: J2.5 (SCK), U3.41 (14_A0_PWM_SCK0)
SCL_TEENSY: R1.2, U2.8 (SCL), U3.46 (19_A5_SCL0_TOUCH), U5.14 (SCL/SCLK)
SDA_TEENSY: R2.2, U2.7 (SDL), U3.45 (18_A4_SDA0_TOUCH), U5.13 (SDA/SDI/SDIO)
TX: J1.5, U3.31 (34_A15_CAN1TX_SDA0)

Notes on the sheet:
MPL3115A2 (Altimeter)
Vdd: power supply connection (1.95-3.6V) CAP: Ext. capacitor GND: Ground Vddio: Digital interface power supply (1.62-3.6V) INT2: Pressure interrupt 2 INT1: Pressure interrupt 1 SDA: I2C serial data SDL: I2C serial clock
Pull-up resistors exist on another part of the schematic.
ADXL345
RADIO (RFM9X LoRa)
POWER INPUT from BMS
GPS
ceramic capacitor preferred
tantalum capacitor preferred see datasheet page 28.
TX RX
(GPS) RX -> TX (Teensy) (GPS) TX -> RX (Teensy)
5V out when powered by USB; 3.3V in when powered by BMS
<HEADER PINS>
TEENSY 3.6
Ratio of R5 to R6 has to be 2.5 to 1 (or rather 2.0 to 0.8) so that VSNS receives 0.8V when BMS_to_sensors drops below 2.8V
Needs to be connected to "pins" 1 and 3 on the footprint
Connect here instead? (Main SCK0 pin)

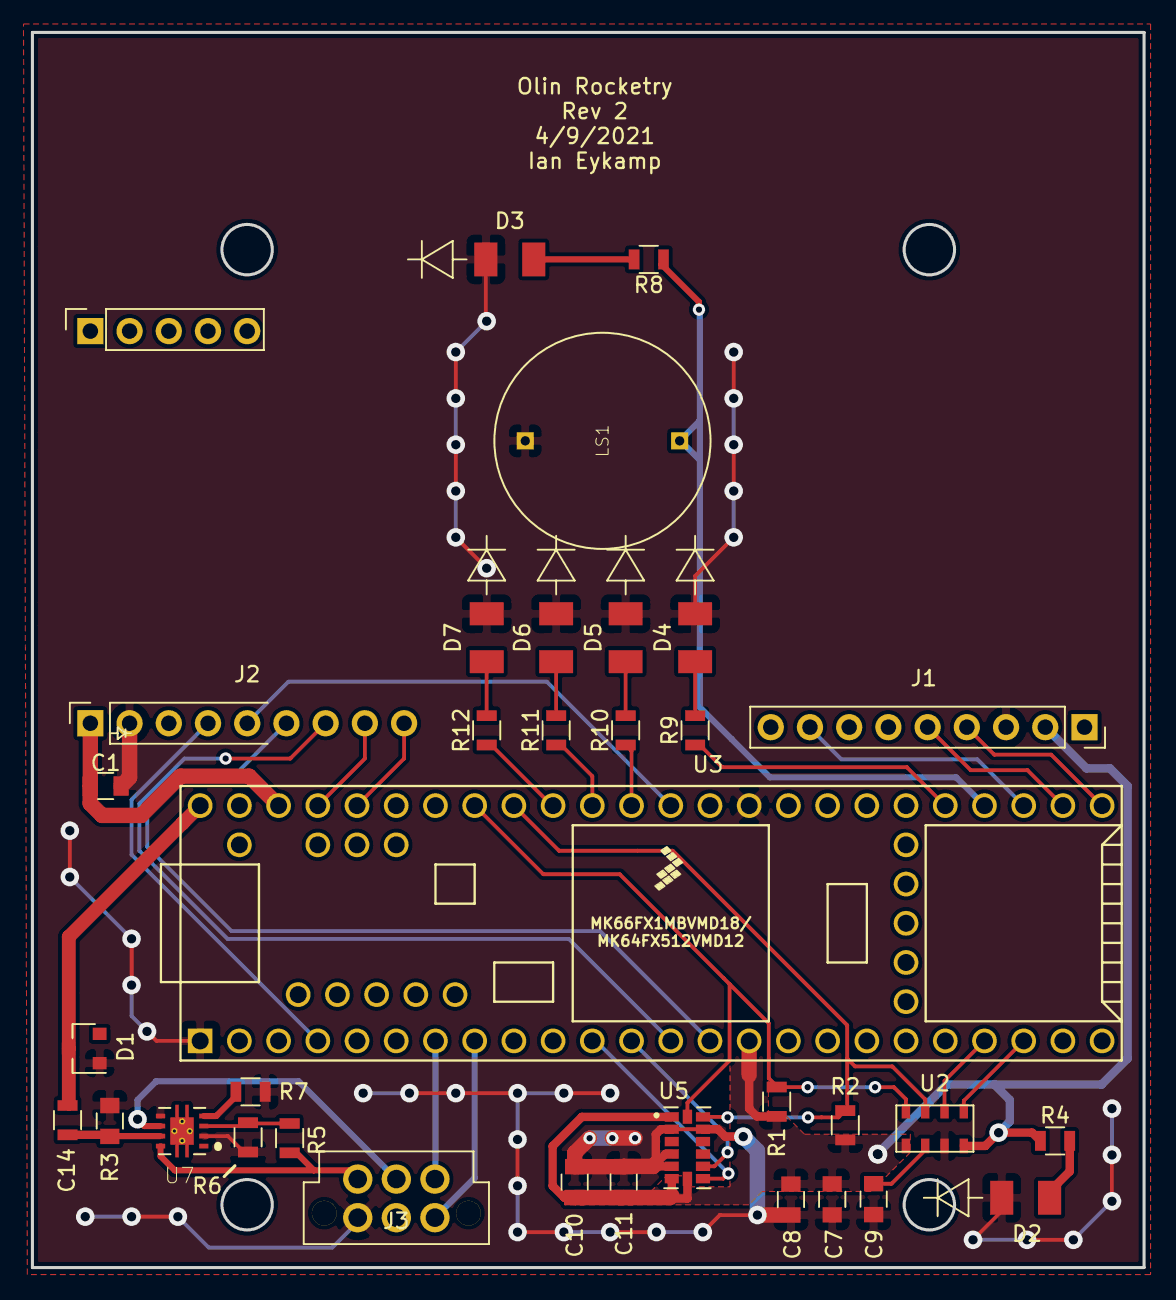
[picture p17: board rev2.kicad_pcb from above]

Board: 2 copper layers, 72.0 x 80.0 mm, 34 parts (1 on the bottom side), 38 nets.

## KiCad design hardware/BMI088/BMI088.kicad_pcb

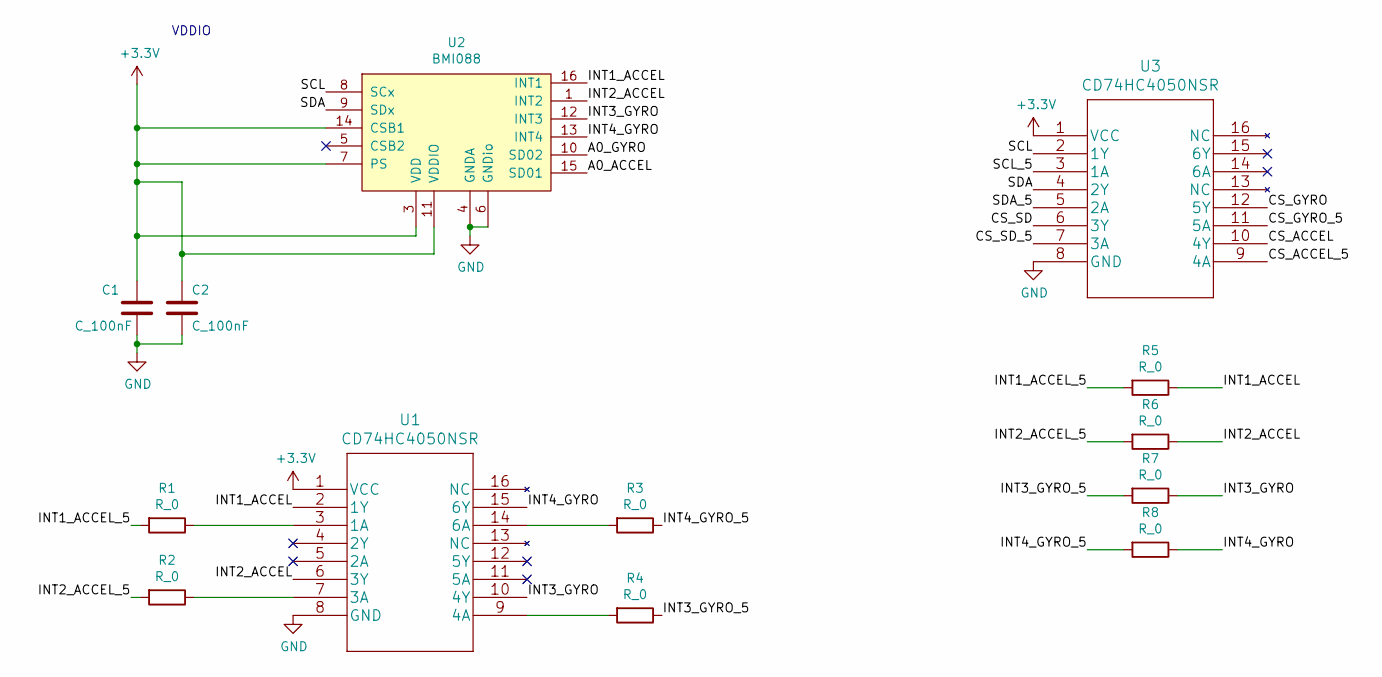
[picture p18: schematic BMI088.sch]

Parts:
C1, C2: C_100nF; C_0603_1608Metric; MPN 1276-6717-1-ND
R1, R2, R3, R4, R5, R6, R7, R8: R_0; R_0603_1608Metric; MPN P0.0GCT-ND
U1, U3: CD74HC4050NSR
U2: BMI088; bmi088

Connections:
+3V3: C1.1, C2.1, U1.1 (VCC), U2.3 (VDD), U2.7 (PS), U2.11 (VDDIO), U2.14 (CSB1), U3.1 (VCC)
/A0_ACCEL: U2.15 (SD01)
/A0_GYRO: U2.10 (SD02)
/CS_ACCEL: U3.10 (4Y)
/CS_ACCEL_5: U3.9 (4A)
/CS_GYRO: U3.12 (5Y)
/CS_GYRO_5: U3.11 (5A)
/CS_SD: U3.6 (3Y)
/CS_SD_5: U3.7 (3A)
/INT1_ACCEL: R5.1, U1.2 (1Y), U2.16 (INT1)
/INT1_ACCEL_5: R1.2, R5.2
/INT2_ACCEL: R6.1, U1.6 (3Y), U2.1 (INT2)
/INT2_ACCEL_5: R2.2, R6.2
/INT3_GYRO: R7.1, U1.10 (4Y), U2.12 (INT3)
/INT3_GYRO_5: R4.1, R7.2
/INT4_GYRO: R8.1, U1.15 (6Y), U2.13 (INT4)
/INT4_GYRO_5: R3.1, R8.2
/SCL: U2.8 (SCx), U3.2 (1Y)
/SCL_5: U3.3 (1A)
/SDA: U2.9 (SDx), U3.4 (2Y)
/SDA_5: U3.5 (2A)
GND: C1.2, C2.2, U1.8 (GND), U2.4 (GNDA), U2.6 (GNDio), U3.8 (GND)
unnamed: R1.1, U1.3 (1A)
unnamed: R2.1, U1.7 (3A)
unnamed: R3.2, U1.14 (6A)
unnamed: R4.2, U1.9 (4A)

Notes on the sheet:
VDDIO

Board: 2 copper layers, 13 parts (0 on the bottom side), 16 nets, no tracks yet.

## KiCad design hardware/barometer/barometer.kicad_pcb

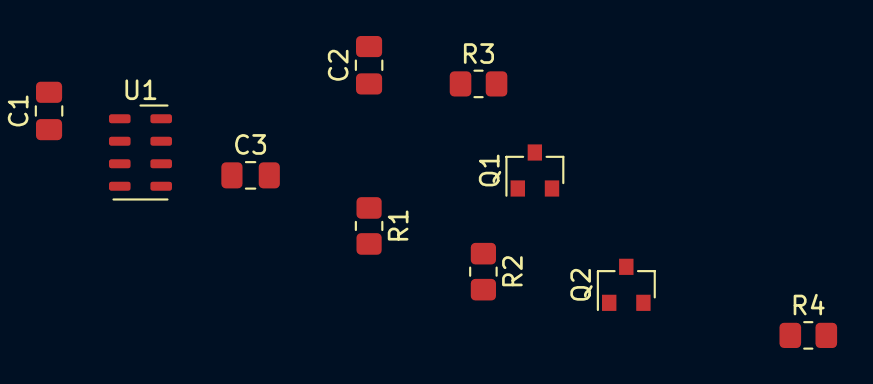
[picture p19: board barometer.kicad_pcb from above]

Board: 2 copper layers, 10 parts (0 on the bottom side), 7 nets, no tracks yet.

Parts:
C1, C3: 100nF; C_0805_2012Metric_Pad1.18x1.45mm_HandSolder
C2: 10uF; C_0805_2012Metric_Pad1.18x1.45mm_HandSolder
Q1, Q2: BSS138; SOT-23
R1, R2, R3, R4: R_10K; R_0805_2012Metric_Pad1.20x1.40mm_HandSolder
U1: MPL3115A2; NXP_LGA-8_3x5mm_P1.25mm_H1.1mm

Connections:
+3V3: Q1.1, Q2.1, R1.1, R2.1
/SCL_3V: Q2.2, R2.2
/SCL_RAW: Q2.3, R4.2
/SDA_3V: Q1.2, R1.2
/SDA_RAW: Q1.3, R3.2
GND: C1.2, C2.1, C2.2, C3.1, C3.2, R3.1, R4.1, U1.1, U1.3
unnamed: C1.1, U1.2

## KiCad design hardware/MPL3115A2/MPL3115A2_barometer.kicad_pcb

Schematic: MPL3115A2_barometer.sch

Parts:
C1, C3: 100n; C_0805_OEM
C2: 10u; C_0805_OEM
TP1: TestPoint; TestPoint_Keystone_5010-5014_Multipurpose
U1: MPL3115A2

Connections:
GND: C1.2, C2.2, C3.2, U1.3
INT1: U1.6
INT2: U1.5
unnamed: C3.1, TP1.1, U1.2
SCL: U1.8
SDL: U1.7
VDDIO: C1.1, C2.1, U1.1, U1.4

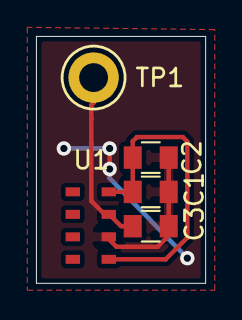
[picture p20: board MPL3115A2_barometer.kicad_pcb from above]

Board: 2 copper layers, 9.4 x 13.7 mm, 5 parts (0 on the bottom side), 3 nets.

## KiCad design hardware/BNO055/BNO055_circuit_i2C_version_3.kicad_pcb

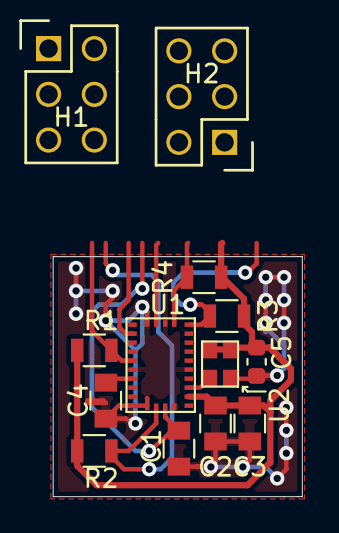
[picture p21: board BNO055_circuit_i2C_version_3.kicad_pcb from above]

Board: 2 copper layers, 13.8 x 13.3 mm, 13 parts (0 on the bottom side), 11 nets.

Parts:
C1, C4: 100nF; C_0805_OEM
C2: 6.8nF; C_0805_OEM
C3: 120nF; C_0805_OEM
C5: 0.01u; C_0603_1608Metric
H1, H2: Header_2x3; Pin_Header_Straight_2x03
R1: Optional 10k; R_0805_OEM
R2: Pull-up 10k; R_0805_OEM
R3, R4: Rpull; R_0805_OEM
U1: BNO055
U2: ASDMB-xxxMHz; ASDK2-32.768KHZ-LR-T3

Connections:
COM3: H2.1, U1.17
GND: C1.2, C2.1, C3.1, C4.2, C5.1, H1.1, U1.2, U1.5, U1.6, U1.10, U1.16, U1.18, U1.25, U2.2
INT: H2.6, U1.14
unnamed: C4.1, U1.9
OptionalOSCinput: U1.27, U2.3
SCL: H2.3, R4.2, U1.19
SDA: H2.5, R3.2, U1.20
VDD: C1.1, H1.3, U1.3
VDDIO: C2.2, C3.2, C5.2, H1.5, R1.1, R2.1, R3.1, R4.1, U1.28, U2.1, U2.4
nBOOT_LOAD_PIN: H2.2, R2.2, U1.4
nRESET: H2.4, R1.2, U1.11

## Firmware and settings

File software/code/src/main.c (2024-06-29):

/**
  ******************************************************************************
  *
  * main function
  * author: coregiu
  *
  *
  ******************************************************************************
**/

#include <controller.h>
/* 71ms per period */
#define READ_PS2_INTVAL_TIME_MS_H   0XFC
#define READ_PS2_INTVAL_TIME_MS_L   0X66

// 默认配置，占空比周期5次， 步长1
struct motor_config g_motor_config = {0XFC, 0X66, 5, 1};

void delay_time_ms(unsigned int mil_sec)
{
	unsigned int i, j;
	for (i = mil_sec; i > 0; i--)
		for (j = 70; j > 0; j--)
			;
}

/**
 * init timer 0.
 */
void init_timer_0()
{
	// init timer0
	TMOD |= 0X01;
    TH0 = g_motor_config.motor_period_h;
    TL0 = g_motor_config.motor_period_l;
	ET0 = 1;
    TR0 = 1;
	EA  = 1; //开启总中断
}

/**
 * init uart.
 */
void init_uart()
{
	// init uart
	TMOD |= 0x20; //用定时器设置串口波特率	   9600
	TH1  = 0xfd;
	TL1  = 0xfd;
	TR1  = 1;
	ES   = 0;
	SCON = 0X50;
	EA   = 1; //开启总中断
}

void main()
{
	delay_time_ms(500);

	init_timer_0();
	init_uart();
	init_modules();
	uart_log_start_info();


	while (1)
	{
		// read ps2 command and set is_has_command/non_motor_cmd_times value.
        struct command_key command_key = {0, 0, MODULE_NULL};

		read_ps2(&command_key);
        // uart_log_hex_data(key_module);
		// executet the commands.
		execute_commands(&command_key);
		delay_time_ms(150);
	}
}

/**
 * timer 0 interrupt function.
 * read ps2 command and execute it by 50ms interval.
 */
void time_0_isr(void) __interrupt 1
{
	// reset number of beginning.
	TH0 = g_motor_config.motor_period_h;
	TL0 = g_motor_config.motor_period_l;

    left_motor_pwm_controller.update_pwm_status();
    right_motor_pwm_controller.update_pwm_status();
}

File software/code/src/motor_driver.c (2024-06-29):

/**
  ******************************************************************************
  *
  * The driver of motor
  * author: coregiu
  *
  * | 按键     | 功能                         | 监控指示灯 |
  * | -------- | ---------------------------- | ---------- |
  * | 左侧上键 | 坦克前进，长按有效，放开停止                  | P0_0       |
  * | 左侧下键 | 坦克后退，长按有效，放开停止                  | P0_1       |
  * | 左侧左键 | 坦克左转，长按有效，放开停止                  | P0_2       |
  * | 左侧右键 | 坦克右转，长按有效，放开停止                  | P0_3       |
  * | 左侧1键  | 顺时针快速调头                              | P0_4       |
  * | 左侧2键  | 逆时针快速调头                              | P0_5       |
  * | 右侧上健 | 加速行驶                                  | P0_0       |
  * | 右侧下键 | 减速行驶                                  | P0_1      |
  * | 右侧左键 | 坦克向左微调80%PWM，长按有效，放开恢复正常行驶  | P0_2       |
  * | 右侧右键 | 坦克向右微调80%PWM，长按有效，放开恢复正常行驶  | P0_3       |
  * | 右侧1键  | 同时按住左侧健时，直接最大速度行驶。 不按左侧健时，微调行驶角度，PWN加20%         | P0_4       |
  * | 右侧2键  | 同时按住左侧健时，直接最小速度行驶。 不按左侧健时，微调行驶角度，PWN减20%         | P0_5       |
  *
  * MOVE command:
  *     key: LEFT_TOP
  *     monitor led: P0_0
  *     gpio:
  *         LEFT_EN = 1
  *         LEFT_MV = 1
  *         LEFT_BK = 0
  *         RIGHT_EN = 1
  *         RIGHT_MV = 1
  *         RIGHT_BK = 0
  *
  * BACK command:
  *     key: LEFT_DOWN
  *     monitor led: P0_1
  *     gpio:
  *         LEFT_EN = 1
  *         LEFT_MV = 0
  *         LEFT_BK = 1
  *         RIGHT_EN = 1
  *         RIGHT_MV = 0
  *         RIGHT_BK = 1
  *
  * TURN LEFT command:
  *     key: LEFT_LEFT
  *     monitor led: P0_2
  *     gpio:
  *         LEFT_EN = 0
  *         LEFT_MV = 0
  *         LEFT_BK = 0
  *         RIGHT_EN = 1
  *         RIGHT_MV = 1
  *         RIGHT_BK = 0
  *
  * TURN RIGHT command:
  *     key: LEFT_RIGHT
  *     monitor led: P0_3
  *     gpio:
  *         LEFT_EN = 1
  *         LEFT_MV = 1
  *         LEFT_BK = 0
  *         RIGHT_EN = 0
  *         RIGHT_MV = 0
  *         RIGHT_BK = 0
  *
  * P2_0 : RIGHT_EN  L298N_EnA
  * P2_1 : RIGHT_MV  L298N_IN2
  * P2_2 : RIGHT_BK  L298N_IN1
  * P2_3 : LEFT_EN   L298N_EnB
  * P2_4 : LEFT_MV   L298N_IN4
  * P2_5 : LEFT_BK   L298N_IN3
  *
  ******************************************************************************
**/
#include <motor_driver.h>
#include <mcs51/8051.h>

// the position of gpio in CAR_STATE_LIST array.
enum gpio_position
{
    LEFT_EN_POSITION  = 0,
    LEFT_MV_POSITION  = 1,
    LEFT_BK_POSITION  = 2,
    RIGHT_EN_POSITION = 3,
    RIGHT_MV_POSITION = 4,
    RIGHT_BK_POSITION = 5
};

// car sate to set to gpio: {LEFT_EN, LEFT_MV, LEFT_BK, RIGHT_EN, RIGHT_MV, RIGHT_BK}
const uchar CAR_STATE_LIST[7][6] = {{0, 0, 0, 0, 0, 0},  // init
                                    {1, 1, 0, 1, 1, 0},  // move
                                    {1, 0, 1, 1, 0, 1},  // back
                                    {0, 0, 0, 1, 1, 0},  // left
                                    {1, 1, 0, 0, 0, 0},  // right
                                    {1, 1, 0, 1, 0, 1},  // left_back
                                    {1, 0, 1, 1, 1, 0}}; // right_back

const uchar NO_PWM = 99;

enum car_run_state current_car_status = STOP;
struct motor_run_state g_left_motor_run_state  = {0, 0, 0};
struct motor_run_state g_right_motor_run_state = {0, 0, 0};
uchar pre_right_cmd;

// 当前系统的占空比，以此占空比来控制电机速度
uchar current_pwm;


void exec_car_state_update(enum car_run_state run_state)
{
    if (current_car_status == run_state)
    {
        return;
    }

    LEFT_EN  = CAR_STATE_LIST[run_state][LEFT_EN_POSITION];
    LEFT_MV  = CAR_STATE_LIST[run_state][LEFT_MV_POSITION];
    LEFT_BK  = CAR_STATE_LIST[run_state][LEFT_BK_POSITION];
    g_left_motor_run_state.pwm_rate = run_state == STOP ? NO_PWM : current_pwm;

    RIGHT_EN = CAR_STATE_LIST[run_state][RIGHT_EN_POSITION];
    RIGHT_MV = CAR_STATE_LIST[run_state][RIGHT_MV_POSITION];
    RIGHT_BK = CAR_STATE_LIST[run_state][RIGHT_BK_POSITION];
    g_right_motor_run_state.pwm_rate = run_state == STOP ? NO_PWM : current_pwm;

    current_car_status = run_state;
}


void init_motor_driver()
{
    pre_right_cmd = COMMAND_NULL;
    current_pwm = NO_PWM;
    exec_car_state_update(STOP);
}

void exec_car_pwm_update(uchar command)
{
    if (pre_right_cmd == command)
    {
        return;
    }

    pre_right_cmd = command;

    switch (command)
        {
        // 加速，占空比逐步提升
        case COMMAND_RIGHT_TOP:
        {
            LED_RIGHT_TOP = !LED_RIGHT_TOP;

            current_pwm += g_motor_config.pwm_change_step;
            current_pwm = current_pwm >= g_motor_config.pwm_period_times ? NO_PWM : current_pwm;

            g_left_motor_run_state.pwm_rate = current_pwm;
            g_right_motor_run_state.pwm_rate = current_pwm;
            break;
        }
        // 减速，占空比逐步下降
        case COMMAND_RIGHT_DOWN:
        {
            LED_RIGHT_DOWN = !LED_RIGHT_DOWN;

            current_pwm = current_pwm == NO_PWM ? g_motor_config.pwm_period_times : current_pwm;
            current_pwm -= g_motor_config.pwm_change_step;
            current_pwm = current_pwm <= g_motor_config.pwm_change_step ? g_motor_config.pwm_change_step : current_pwm;

            g_left_motor_run_state.pwm_rate = current_pwm;
            g_right_motor_run_state.pwm_rate = current_pwm;
            break;
        }
        // 向左微调
        case COMMAND_RIGHT_LEFT:
        {
            LED_RIGHT_LEFT = !LED_RIGHT_LEFT;
            g_left_motor_run_state.pwm_rate = current_pwm > tune_pwm_step ? (current_pwm == NO_PWM ? g_motor_config.pwm_period_times : current_pwm) - tune_pwm_step  : 0;
            g_right_motor_run_state.pwm_rate = current_pwm;
            break;
        }
        // 向右微调
        case COMMAND_RIGHT_RIGHT:
        {
            LED_RIGHT_RIGHT = !LED_RIGHT_RIGHT;
            g_left_motor_run_state.pwm_rate = current_pwm;
            g_right_motor_run_state.pwm_rate = current_pwm > tune_pwm_step ? (current_pwm == NO_PWM ? g_motor_config.pwm_period_times : current_pwm) - tune_pwm_step  : 0;
            break;
        }
        // 全速前进，占空比拉满
        case COMMAND_RIGHT_1:
        {
            LED_LEFT_LEFT = !LED_LEFT_LEFT;
            current_pwm = NO_PWM;
            g_left_motor_run_state.pwm_rate = current_pwm;
            g_right_motor_run_state.pwm_rate = current_pwm;
            break;
        }
        // 最低速前进
        case COMMAND_RIGHT_2:
        {
            LED_LEFT_RIGHT = !LED_LEFT_RIGHT;
            current_pwm = g_motor_config.pwm_change_step;
            g_left_motor_run_state.pwm_rate = current_pwm;
            g_right_motor_run_state.pwm_rate = current_pwm;
            break;
        }
        // 恢复当前占空比行驶
        case COMMAND_NULL:
        {
            g_left_motor_run_state.pwm_rate  = current_pwm;
            g_right_motor_run_state.pwm_rate = current_pwm;
            break;
        }
        default:
            break;
        }

}
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

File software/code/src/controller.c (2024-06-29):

/**
  ******************************************************************************
  *
  * main controller
  * author: coregiu
  *
  *
  ******************************************************************************
**/

#include <controller.h>

/**
 * init uart and all receive modules
 *
 */
void init_modules()
{
    pwm_manager.init();
    motor_driver.init();
}

/**
 * receive ps2 data, convert to commands,
 * and notify modules to execute commands;
 *
 */
void execute_commands(struct command_key *command_key)
{
    notify_all(command_key);
}

/**
 * notify modules to execute the commands.
 * car_module: the module of car, such as motor, music, led
 * car_cmd: the command
 *
 */
void notify_all(struct command_key *command_key)
{
    switch (command_key->exe_module)
    {
    case MODULE_MOTOR:
    {
        motor_driver.update_state(command_key);
        break;
    }
    case MODULE_PWM:
    {
        pwm_manager.update_state(command_key);
        break;
    }
    case MODULE_NULL:
        motor_driver.update_state(command_key);
        pwm_manager.update_state(command_key);
        break;
    default:
        break;
    }
}

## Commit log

2023-05-24 init ruke project
    [ruke.kicad_pcb, ruke.kicad_sch]
2023-06-03 fix key module to control right key
    [command_receiver.h, controller.c, main.c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]
2023-06-03 fix ram size limit problem
    [command_receiver.h, controller.c, log.c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]
2023-06-03 fix bug of key module read.
    [command_receiver.h, controller.c, main.c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]
2023-06-03 fix bug of increase step
    [main.c, motor_driver.c]
2023-06-05 fix to command key struct.
    [command_receiver.h, controller.c, main.c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]
2024-06-24 fix bug of tune
    [motor_driver.c, ps2_receiver.c]
2024-06-25 fix design of state.
    [motor_driver.c]
2024-06-29 change pwm rate to global control.
2024-07-07 change to 4 drivers.
